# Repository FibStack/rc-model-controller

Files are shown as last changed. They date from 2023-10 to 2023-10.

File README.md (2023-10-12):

# RC Transmitter Receiver System

## Overview

This project has the design files for a custom Remote Control (RC) system that you can use to control different models. The design files include:

- Schematics and PCB design for the transmitter and receiver boards.
- The source code for the microcontrollers on the transmitter and receiver boards.
- A sample 3D printable model for an RC car.

Please note that this is just the initial proof of concept, and more updates are on the way to make it even better.

## Project organization

- **hardware/** - In this folder, you'll find the circuit schematics and PCB design files for both the receiver and transmitter boards.
- **software/attiny824-transmiter** - This contains the source code for the ATTiny824 chip on the transmitter board.
- **software/attiny824-receiver** - Here, you'll find the source code for the ATTiny824 chip on the receiver board.
- **rc-car-frame.FCStd** - This file holds a 3D model of an RC car frame that we used for testing in this project.

## Development tools

- **[Microchip Studio 7.0](https://www.microchip.com/en-us/tools-resources/develop/microchip-studio)**: The IDE for writing and building source code for the ATTiny chip. We also use this tool to flash the chips.
- **[ATMEL-ICE](https://www.microchip.com/en-us/development-tool/ATATMEL-ICE)**: Hardware tool for flashing ATTiny chips.
- **[KiCad EDA](https://www.kicad.org/)**: The application for schematic and PCB design.
- **[FreeCAD](https://www.freecad.org/)**: The application for parametric desing used to desing the model.

To build the ATTiny824 firmware, open the project in Microchip Studio. Build the solution to generate the `*.HEX` file. Next, use the appropriate tool available to flash the chip.

## BOM
| # | Components | Recommended models | Footprint | Quantity |
| --- | --- | --- | --- | --- |
| 1 | PCB | Recommended two-layer PCB board of 1.6 mm thickness | | 1 |
| 2 | U1, U2 | ATtiny824 | SOIC-14 | 2 |
| 3 | C1, C2 | 100nF | 0603 (1608 metric) | 2 |
| 4 | D1, D3 | SMD LED | 0603 (1608 metric) | 2 |
| 5 | D2, D4 | SMD Generic diode | MicroMELF | 2 |
| 6 | Q1-Q6 | 2N7002 | SOT-23 | 6 |
| 7 | R1, R2, R4, R5, R6, R7, R9, R12, R13, R18, R19, R20  | 10K | 0603 (1608 metric) | 12 |
| 8 | R3, R14  | 470 | 0603 (1608 metric) | 2 |
| 9 | R8, R10, R11, R15, R16, R17  | 100 | 0603 (1608 metric) | 6 |
| 10 | RV1 | 10K Slide Potentiometer | PTA1543 | 1 |
| 11 | RV2 | 10K Potentiometer | T-16H Single Horizontal | 1 |
| 12 | SW1, SW2, SW3, SW4, SW5, SW6 | SPDT Slide Switch | P2.54mm | 6 |
| 13 | J1 | Male Header Connector, 1x3, pitch 2.54mm | 	1x3 - P2.54mm | 1 |
| 14 | J2, J5, J6, J7, J9, J10, J11, J12, J13, J14, J15, J17, J18, J19 | Male Header Connector, 1x2, pitch 2.54mm | 	1x2 - P2.54mm | 14 |
| 15 | J3, J16 | Male Header Connector, 2x3, pitch 2.54mm | 	2x3 - P2.54mm | 2 |
| 16 | J8 | Male Header Connector, 1x4, pitch 2.54mm | 	1x4 - P2.54mm | 1 |

## Documentation

For more detailed information about the project, please visit the [project page](https://fibstack.com/projects/rc-model-controller/).

## License Information
This product is open source!

Please review the LICENSE.md file for license information. Distributed as-is; no warranty is given.

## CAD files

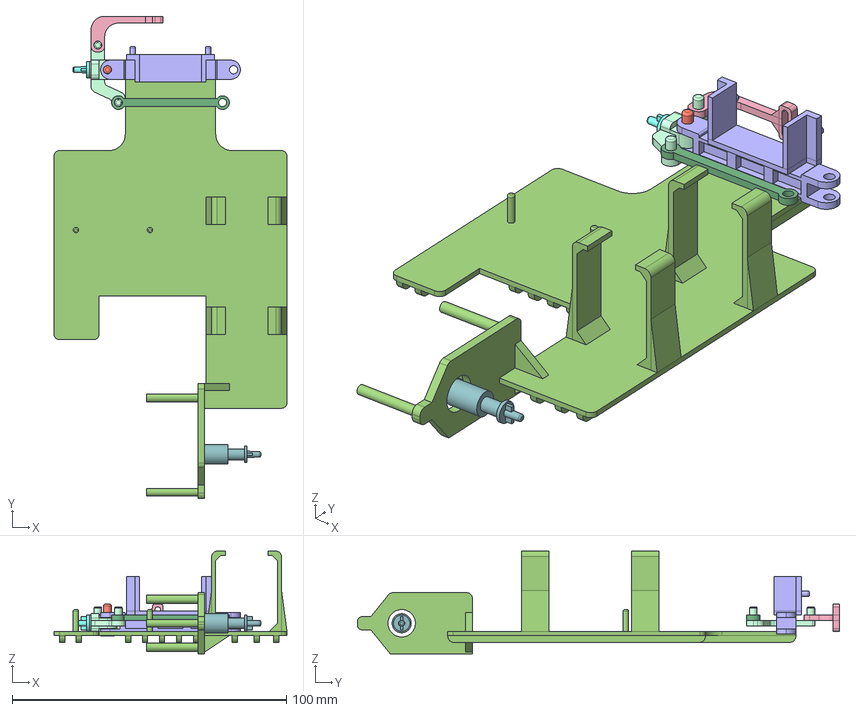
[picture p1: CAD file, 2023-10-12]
rc-car-frame.FCStd
85.0 x 176.0 x 37.5 mm
bearing-ref
steering-knuckle
axle-servo-motor-holder
track-rod
pin1
front-wheel-connector
back-wheel-connector
frame
drag-link-arm

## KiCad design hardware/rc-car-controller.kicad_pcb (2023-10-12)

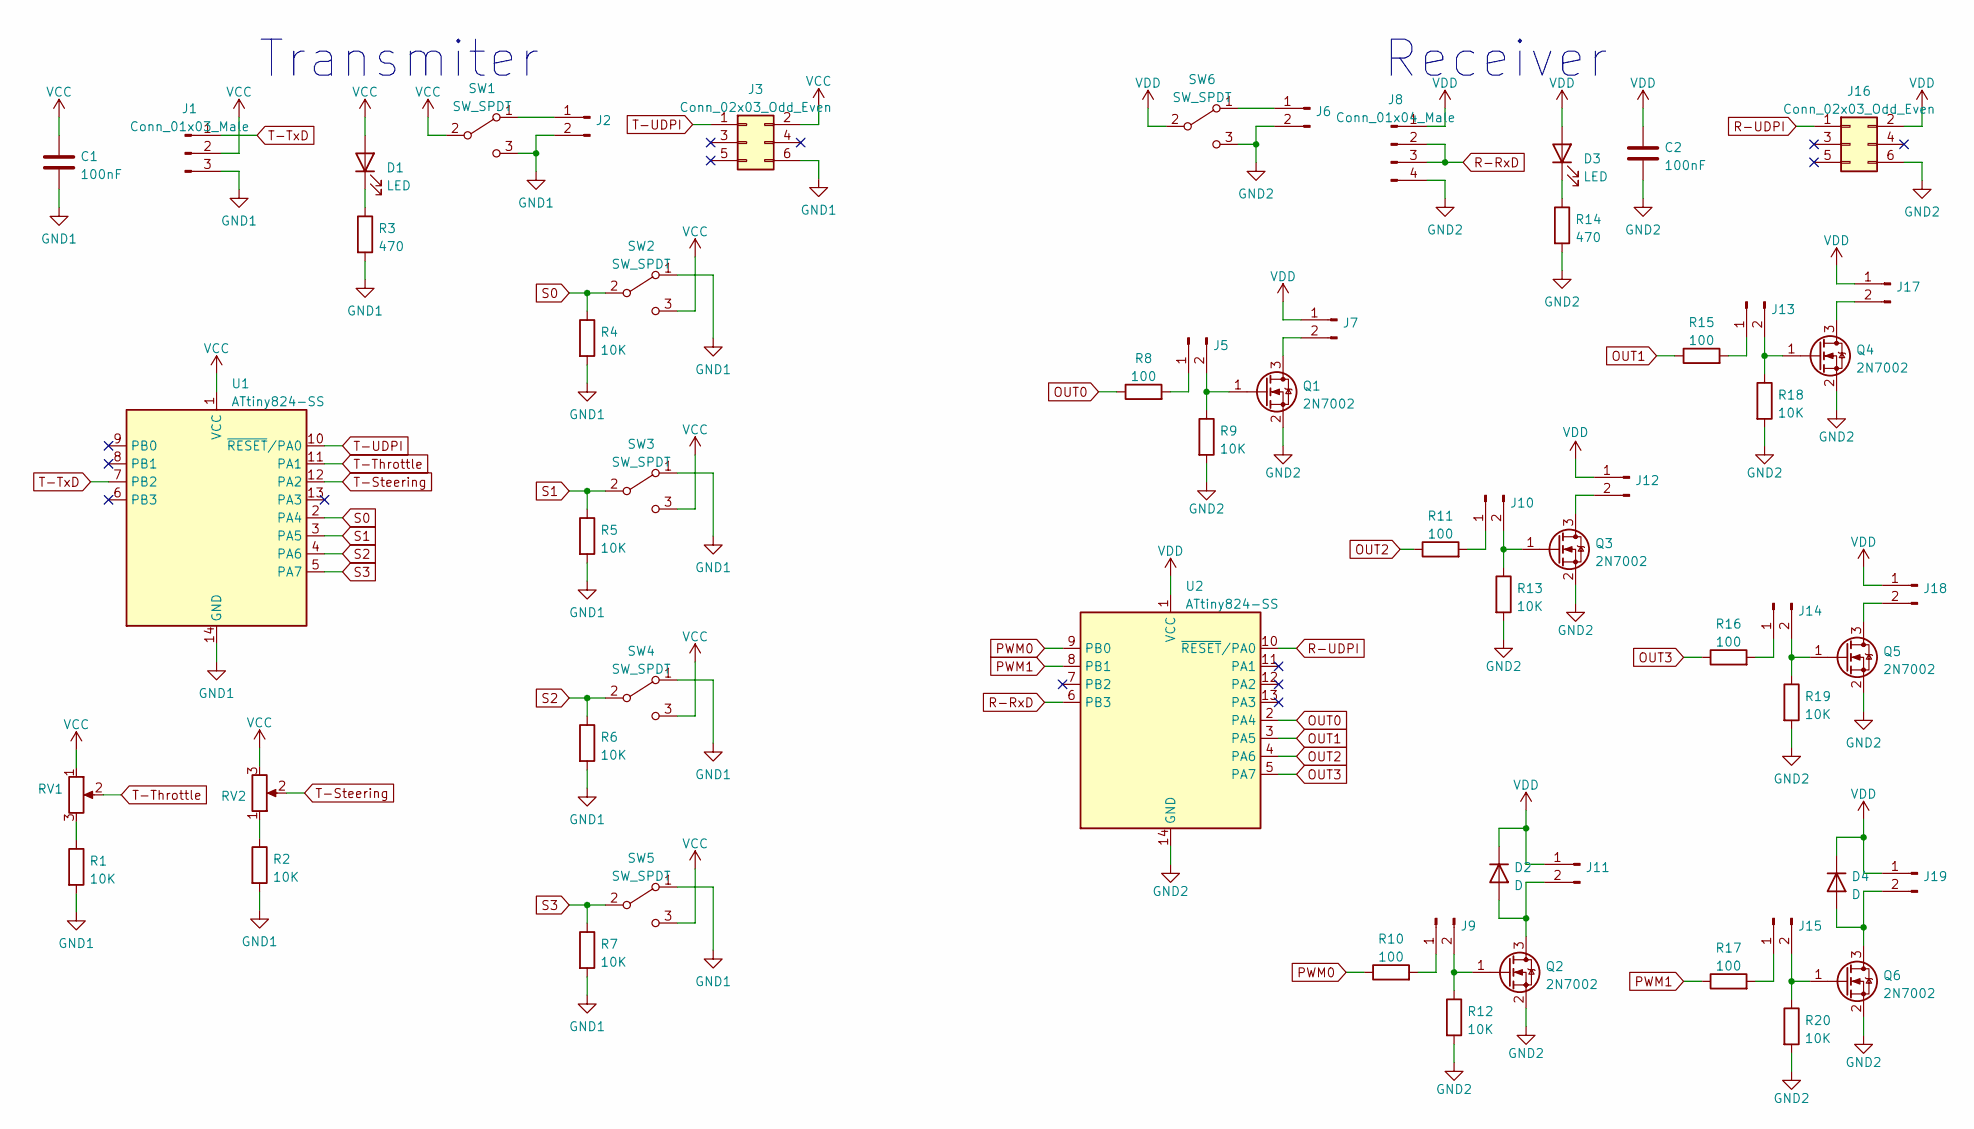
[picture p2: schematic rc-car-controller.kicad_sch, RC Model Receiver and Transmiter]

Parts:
C1, C2: 100nF; C_0603_1608Metric
D1, D3: LED; D_0603_1608Metric
D2, D4: D; D_MicroMELF
J1: Conn_01x03_Male; PinHeader_1x03_P2.54mm_Vertical
J2, J5, J6, J7, J9, J10, J11, J12, J13, J14, J15, J17, J18, J19: Conn_01x02_Male; PinHeader_1x02_P2.54mm_Vertical
J3, J16: Conn_02x03_Odd_Even; PinHeader_2x03_P2.54mm_Vertical
J8: Conn_01x04_Male; PinHeader_1x04_P2.54mm_Vertical
Q1, Q2, Q3, Q4, Q5, Q6: 2N7002; SOT-23
R1, R2, R4, R5, R6, R7, R9, R12, R13, R18, R19, R20: 10K; R_0603_1608Metric
R3, R14: 470; R_0603_1608Metric
R8, R10, R11, R15, R16, R17: 100; R_0603_1608Metric
RV1: R_Potentiometer; Potentiometer_Bourns_PTA1543_Single_Slide
RV2: R_Potentiometer; Potentiometer_Piher_T-16H_Single_Horizontal
SW1, SW2, SW3, SW4, SW5, SW6: SW_SPDT; PinHeader_1x03_P2.54mm_Vertical
U1, U2: ATtiny824-SS; SOIC-14_3.9x8.7mm_P1.27mm

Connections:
GND1: C1.2, J1.3, J2.2, J3.6, R1.2, R2.2, R3.2, R4.2, R5.2, R6.2, R7.2, SW1.3 (C), SW2.1 (A), SW3.1 (A), SW4.1 (A), SW5.1 (A), U1.14 (GND)
GND2: C2.2, J6.2, J8.4, J16.6, Q1.2 (S), Q2.2 (S), Q3.2 (S), Q4.2 (S), Q5.2 (S), Q6.2 (S), R9.2, R12.2, R13.2, R14.2, R18.2, R19.2, R20.2, SW6.3 (C), U2.14 (GND)
unnamed: D1.1 (K), R3.1
unnamed: D2.2 (A), J11.2, Q2.3 (D)
unnamed: D3.1 (K), R14.1
unnamed: D4.2 (A), J19.2, Q6.3 (D)
unnamed: J2.1, SW1.1 (A)
unnamed: J5.1, R8.2
unnamed: J5.2, Q1.1 (G), R9.1
unnamed: J6.1, SW6.1 (A)
unnamed: J7.2, Q1.3 (D)
unnamed: J9.1, R10.2
unnamed: J9.2, Q2.1 (G), R12.1
unnamed: J10.1, R11.2
unnamed: J10.2, Q3.1 (G), R13.1
unnamed: J12.2, Q3.3 (D)
unnamed: J13.1, R15.2
unnamed: J13.2, Q4.1 (G), R18.1
unnamed: J14.1, R16.2
unnamed: J14.2, Q5.1 (G), R19.1
unnamed: J15.1, R17.2
unnamed: J15.2, Q6.1 (G), R20.1
unnamed: J17.2, Q4.3 (D)
unnamed: J18.2, Q5.3 (D)
unnamed: R1.1, RV1.3
unnamed: R2.1, RV2.1
OUT0: R8.1, U2.2 (PA4)
OUT1: R15.1, U2.3 (PA5)
OUT2: R11.1, U2.4 (PA6)
OUT3: R16.1, U2.5 (PA7)
PWM0: R10.1, U2.9 (PB0)
PWM1: R17.1, U2.8 (PB1)
R-RxD: J8.2, J8.3, U2.6 (PB3)
R-UDPI: J16.1, U2.10 (~RESET/PA0)
S0: R4.1, SW2.2 (B), U1.2 (PA4)
S1: R5.1, SW3.2 (B), U1.3 (PA5)
S2: R6.1, SW4.2 (B), U1.4 (PA6)
S3: R7.1, SW5.2 (B), U1.5 (PA7)
T-Steering: RV2.2, U1.12 (PA2)
T-Throttle: RV1.2, U1.11 (PA1)
T-TxD: J1.1, U1.7 (PB2)
T-UDPI: J3.1, U1.10 (~RESET/PA0)
VCC: C1.1, D1.2 (A), J1.2, J3.2, RV1.1, RV2.3, SW1.2 (B), SW2.3 (C), SW3.3 (C), SW4.3 (C), SW5.3 (C), U1.1 (VCC)
VDD: C2.1, D2.1 (K), D3.2 (A), D4.1 (K), J7.1, J8.1, J11.1, J12.1, J16.2, J17.1, J18.1, J19.1, SW6.2 (B), U2.1 (VCC)

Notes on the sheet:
Receiver
Transmiter

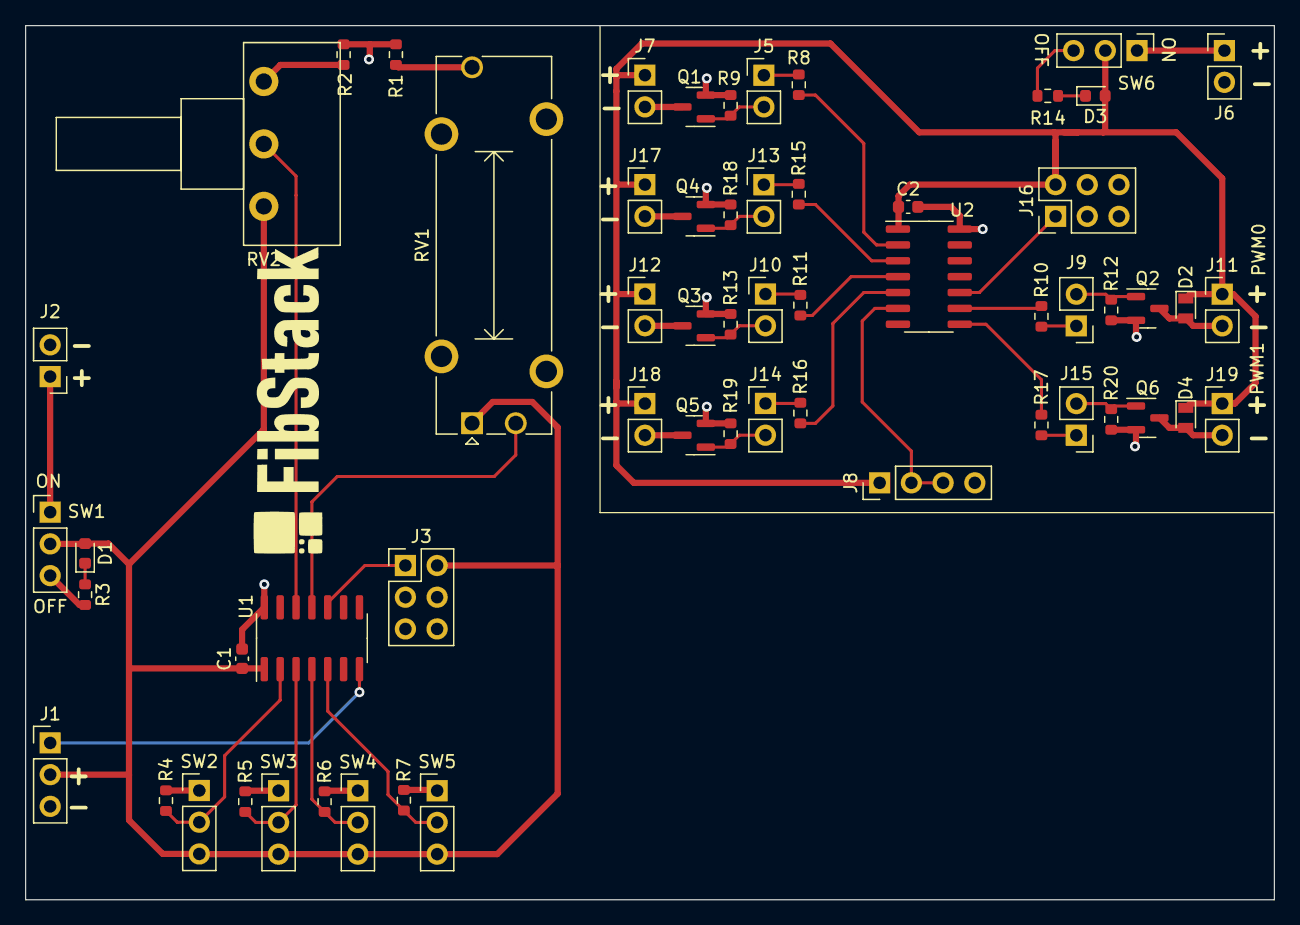
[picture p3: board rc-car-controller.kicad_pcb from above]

Board: 2 copper layers, 100.0 x 70.0 mm, 60 parts (0 on the bottom side), 44 nets.

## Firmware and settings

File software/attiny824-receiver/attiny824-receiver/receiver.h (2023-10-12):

/*
* Copyright (c) 2023, FibStack
* All rights reserved.
*
* This source code is licensed under the MIT license found in the
* LICENSE file in the root directory of this source tree.
*/

#ifndef RECEIVER_H_
#define RECEIVER_H_

#define F_CPU 3333333
#define USART0_BAUD_RATE(BAUD_RATE) ((float)(F_CPU * 64 / (16 * (float)BAUD_RATE)) + 0.5)
#define DEFAULT_STEERING 127
#define DEFAULT_THROTTLE 0
#define STEERING_OFFSET 13
#define STEERING_RANGE 13

extern void USART0_init();
extern uint8_t USART0_read();
extern void PORTA_init();
extern void TCA0_init();

extern uint8_t throttle;
extern uint8_t steering;
extern uint8_t outputs;

extern uint8_t crc8_table[256];
extern uint8_t crc_8(uint8_t *data, uint8_t len);
#endif /* RECEIVER_H_ */

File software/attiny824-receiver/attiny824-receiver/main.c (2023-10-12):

/*
* Copyright (c) 2023, FibStack
* All rights reserved.
*
* This source code is licensed under the MIT license found in the
* LICENSE file in the root directory of this source tree.
*/
#include <avr/io.h>
#include "receiver.h"

/************************************************************************/
/*                              RECEIVER                                */
/************************************************************************/

int main(void)
{
	USART0_init();
	PORTA_init();
	TCA0_init();
	
    while(1)
    {
		uint8_t byte = USART0_read();
		if (byte == 0xFF)
		{
			// Start byte has been read, read the other values
			throttle =  USART0_read();
			steering =  USART0_read();
			outputs = USART0_read();
			uint8_t crc_received = USART0_read();
			uint8_t data[3] = {throttle, steering, outputs};
			uint8_t crc_computed = crc_8(data, 3);
			if ( crc_received == crc_computed)
			{
				PORTA.OUT = outputs << 4;
				TCA0.SPLIT.LCMP0 = throttle;
				TCA0.SPLIT.LCMP1 = STEERING_OFFSET + (steering * STEERING_RANGE/255);
			}
			
		}
    }
}

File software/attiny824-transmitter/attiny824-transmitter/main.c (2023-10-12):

/*
* Copyright (c) 2023, FibStack
* All rights reserved.
*
* This source code is licensed under the MIT license found in the
* LICENSE file in the root directory of this source tree.
*/

#include <avr/io.h>
#include <avr/interrupt.h>
#include "transmitter.h"

/************************************************************************/
/*                            TRANSMITTER                               */
/************************************************************************/

ISR(PORTA_PORT_vect)
{
	if((PA4_INTERRUPT) | (PA5_INTERRUPT) | (PA6_INTERRUPT) | (PA7_INTERRUPT)) {
		switch_state = PORTA.IN >> 4;
		PORTA.INTFLAGS &= PIN4_bm;
		PORTA.INTFLAGS &= PIN5_bm;
		PORTA.INTFLAGS &= PIN6_bm;
		PORTA.INTFLAGS &= PIN7_bm;
	}
}

ISR(ADC0_RESRDY_vect)
{
	ADC0_process();
}

int main(void)
{
	USART0_init();
	PORTA_init();
	ADC0_init();
	switch_state = PORTA.IN >> 4;
	sei();
	
	ADC0_start();
	
	while(1)
	{
		USART0_sendByte(0xFF);
		USART0_sendByte(throttle);
		USART0_sendByte(steering);
		USART0_sendByte(switch_state);
		uint8_t data[3] = {throttle, steering, switch_state};
		USART0_sendByte(crc_8(data, 3));
	}
}

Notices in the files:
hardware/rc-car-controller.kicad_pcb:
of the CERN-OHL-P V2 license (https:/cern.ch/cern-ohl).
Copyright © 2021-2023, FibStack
